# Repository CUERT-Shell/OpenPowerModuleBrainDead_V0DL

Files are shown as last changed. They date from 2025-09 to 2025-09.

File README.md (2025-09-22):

# OpenPowerModule

Kicad Design 
You can view on https://kicanvas.org (for non kicad users)

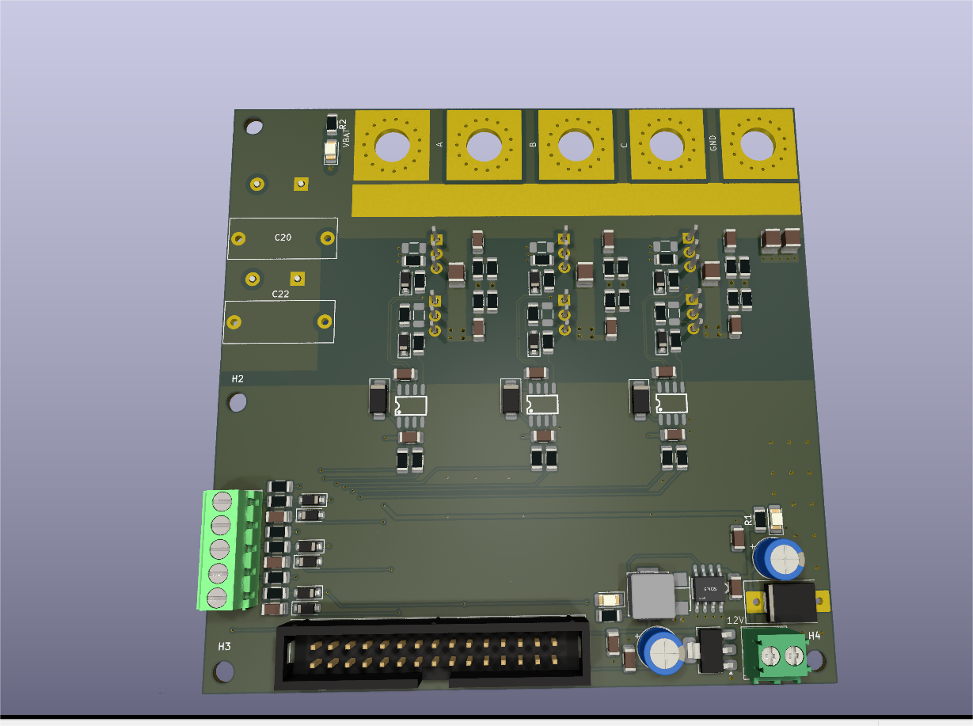
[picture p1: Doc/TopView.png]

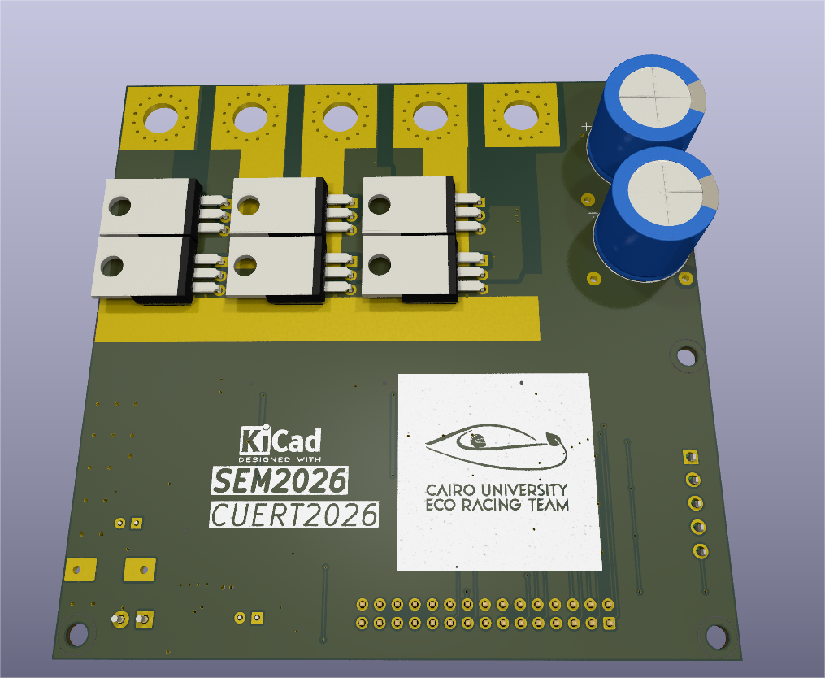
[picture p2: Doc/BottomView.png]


Minimal BLDC drive hardware (without microcontroller)

### The hardware 
* 3phase H-bridge and all its related circuitry (MGD , Snubber , decoupling , etc)
* Hall Sensor Conditioning Circuits
* IDC-2x15 Connector to be interfaced with a controller/MCU
* 12V-->5V buck converter , 3.3V LDO

### Repo Structure
* Main directory : design files
* Production directory : Gerbers and Bom
* LIB : Project Components library
* Doc : Design Reference , guide , step file , etc...

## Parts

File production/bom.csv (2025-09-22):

Designator | Footprint | Quantity | Value | LCSC Part #
C1, C57, C63, C65 | 1206 | 4 | 10u 50V | C13585
C10, C19, C21, C31, C49 | 1210 | 5 | 10uF 100V | C5156756
C12, C2, C3 | 1206 | 3 | 10uF 50V | C7432781
C23, C24, C4, C41, C42, C5 | 1206 | 6 | 470pF | C377098
C27, C29, C44, C45, C7, C9 | 1206 | 6 | 3nF 100V | C7393993
C34, C40, C48 | 1206 | 3 | 220nF 100V | C377088
C61, C67, C69 | 1206 | 3 | 100n 50V | C24497
D10, D11, D19, D20, D26, D27, D28, D29, D5, D6, D7, D8 | D_SOD-123 | 12 | D_Schottky | C181204
D12, D13, D9 | D_SMA | 3 | SS110 | C432299
D16 | SMA_L4.3-W2.6-LS5.2-RD | 1 | SS34_C8678 | C8678
D25, D3, D4 | 1206 | 3 | LED RED | C965822
L1 | IND-SMD_L7.1-W6.6_H5.0 | 1 | SMMS0650-680M | C2894721
Q1, Q2, Q3, Q4, Q5, Q6 | TO-220-3_Horizontal_TabUp | 6 | IRF1407 | C33129604
R1, R10, R2, R21, R22, R31, R32, R45, R51, R54, R9 | 1206 | 11 | 10k | C17902
R13, R14, R15, R16, R19, R20, R25, R26, R27, R28, R29, R3, R30, R35, R36, R37, R38, R4 | 1206 | 18 | 10 | C137208
R17, R18, R46, R5, R52, R55, R6, R7, R8 | 1206 | 9 | 100 | C113307
R53 | 1206 | 1 | 1k | C2907440
U1, U2, U3 | SOP-8_L4.9-W3.9-P1.27-LS6.0-BL | 3 | EG2131_C5240691 | C5240691
U4 | SOIC-8_L5.0-W4.0-P1.27-LS6.0-BL | 1 | XL1509-5.0E1 | C61063
U6 | SOT-223-3_TabPin2 | 1 | AMS1117-3.3 | C347222

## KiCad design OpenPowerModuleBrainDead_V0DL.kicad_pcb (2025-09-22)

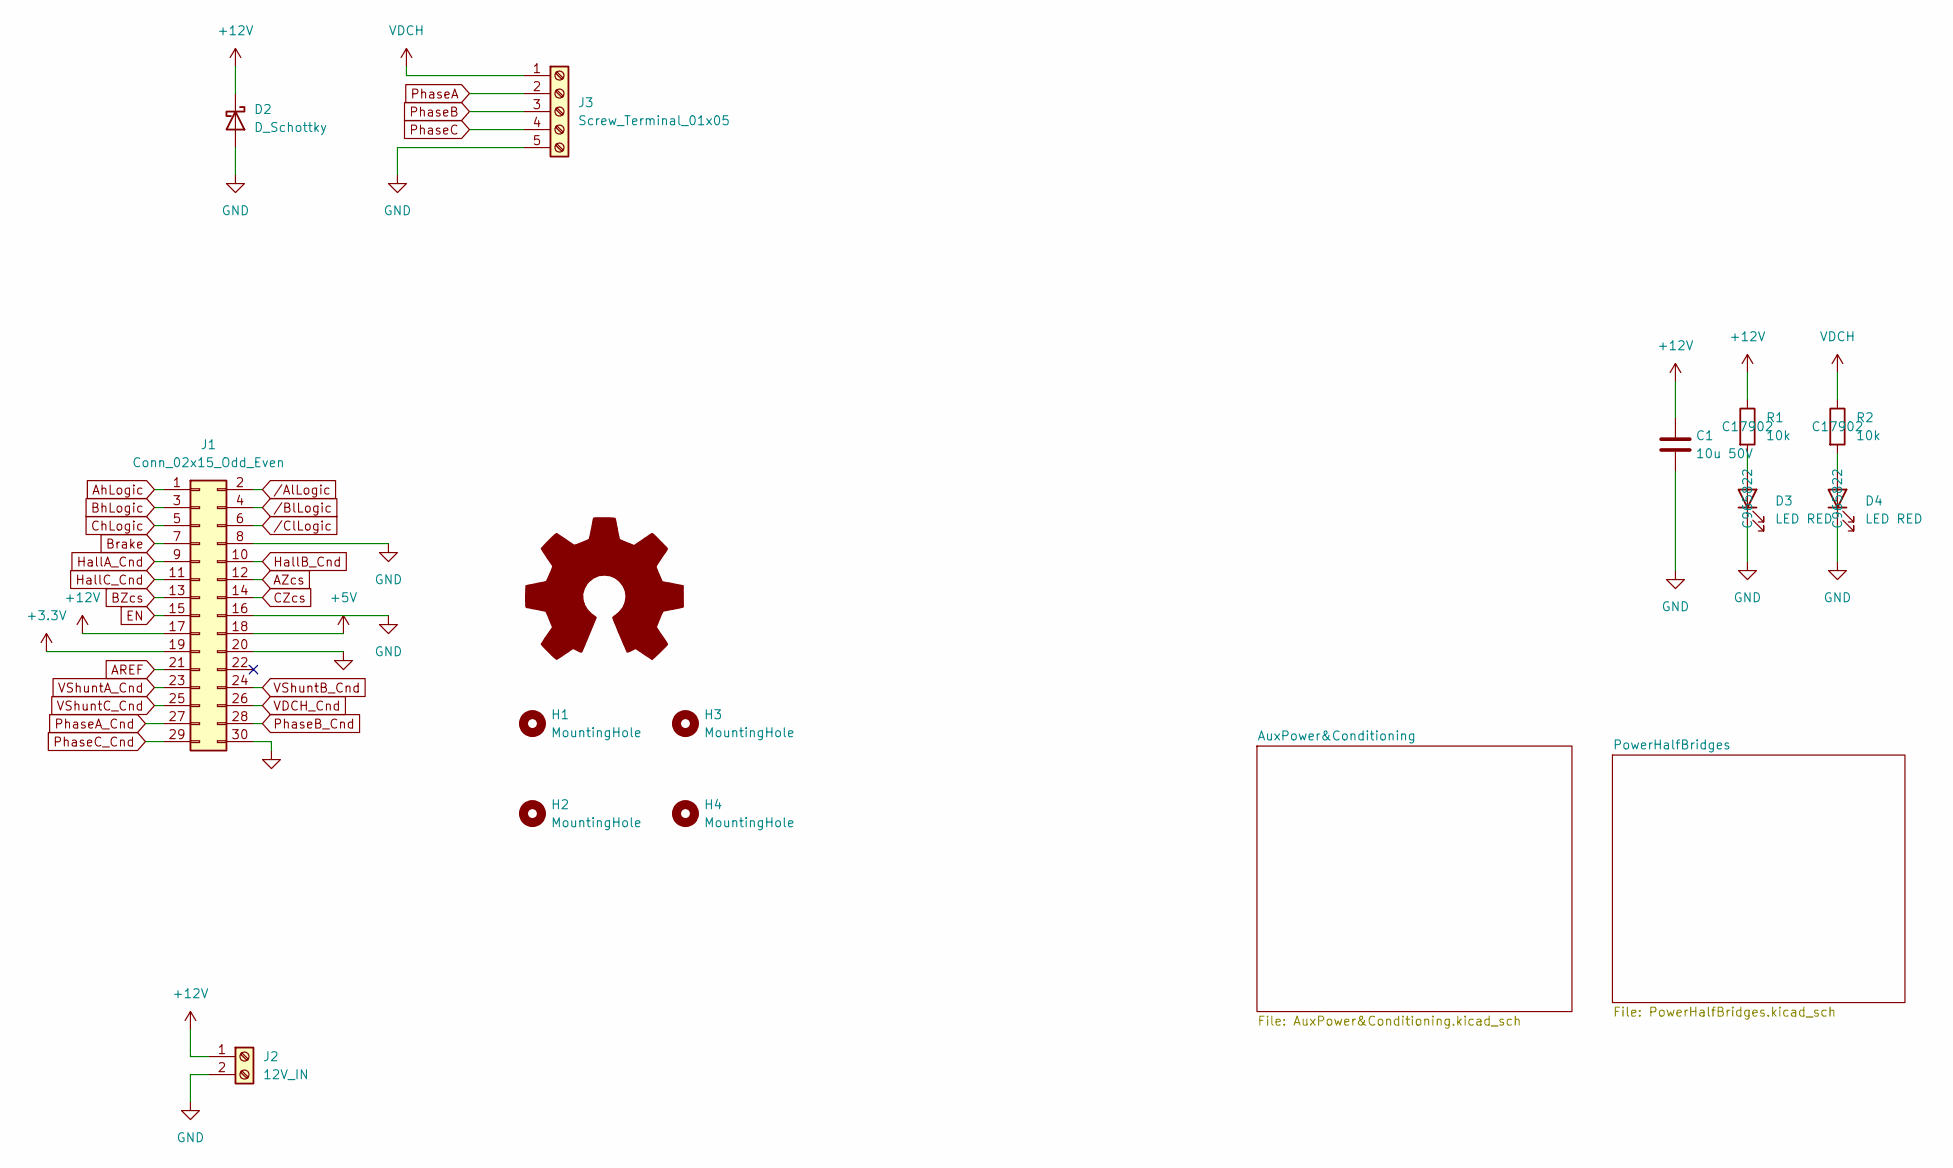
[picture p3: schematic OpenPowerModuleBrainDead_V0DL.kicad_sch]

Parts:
C1: 10u 50V; C_1206_3216Metric; LCSC Part C13585
D2: D_Schottky; D_SMC-RM10_Universal_Handsoldering
D3, D4: LED RED; LED_1206_3216Metric_Pad1.42x1.75mm_HandSolder; LCSC Part C965822
H1, H2, H3, H4: MountingHole; MountingHole_3.2mm_M3_DIN965
H5: Logo_Open_Hardware_Large; MadeWithKicad
J1: Conn_02x15_Odd_Even; IDC-Header_2x15_P2.54mm_Vertical
J2: 12V_IN; TerminalBlock_Phoenix_PT-1,5-2-3.5-H_1x02_P3.50mm_Horizontal
J3: Screw_Terminal_01x05; PowerConn_01x05_P20
R1, R2: 10k; R_1206_3216Metric; LCSC Part C17902

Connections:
+3.3V: J1.19; also elsewhere on the board
+5V: J1.18; also elsewhere on the board
+12V: C1.1, D2.1 (K), J1.17, J2.1, R1.1; also elsewhere on the board
AREF: J1.21
AZcs: J1.12
AhLogic: J1.1; also elsewhere on the board
BZcs: J1.13
BhLogic: J1.3; also elsewhere on the board
Brake: J1.7
CZcs: J1.14
ChLogic: J1.5; also elsewhere on the board
EN: J1.15
GND: C1.2, D2.2 (A), D3.1 (K), D4.1 (K), J1.8, J1.16, J1.20, J1.30, J2.2, J3.5; also elsewhere on the board
HallA_Cnd: J1.9; also elsewhere on the board
HallB_Cnd: J1.10; also elsewhere on the board
HallC_Cnd: J1.11; also elsewhere on the board
unnamed: D3.2 (A), R1.2
unnamed: D4.2 (A), R2.2
PhaseA: J3.2; also elsewhere on the board
PhaseA_Cnd: J1.27
PhaseB: J3.3; also elsewhere on the board
PhaseB_Cnd: J1.28
PhaseC: J3.4; also elsewhere on the board
PhaseC_Cnd: J1.29
VDCH: J3.1, R2.1; also elsewhere on the board
VDCH_Cnd: J1.26
VShuntA_Cnd: J1.23
VShuntB_Cnd: J1.24
VShuntC_Cnd: J1.25
/AlLogic: J1.2; also elsewhere on the board
/BlLogic: J1.4; also elsewhere on the board
/ClLogic: J1.6; also elsewhere on the board

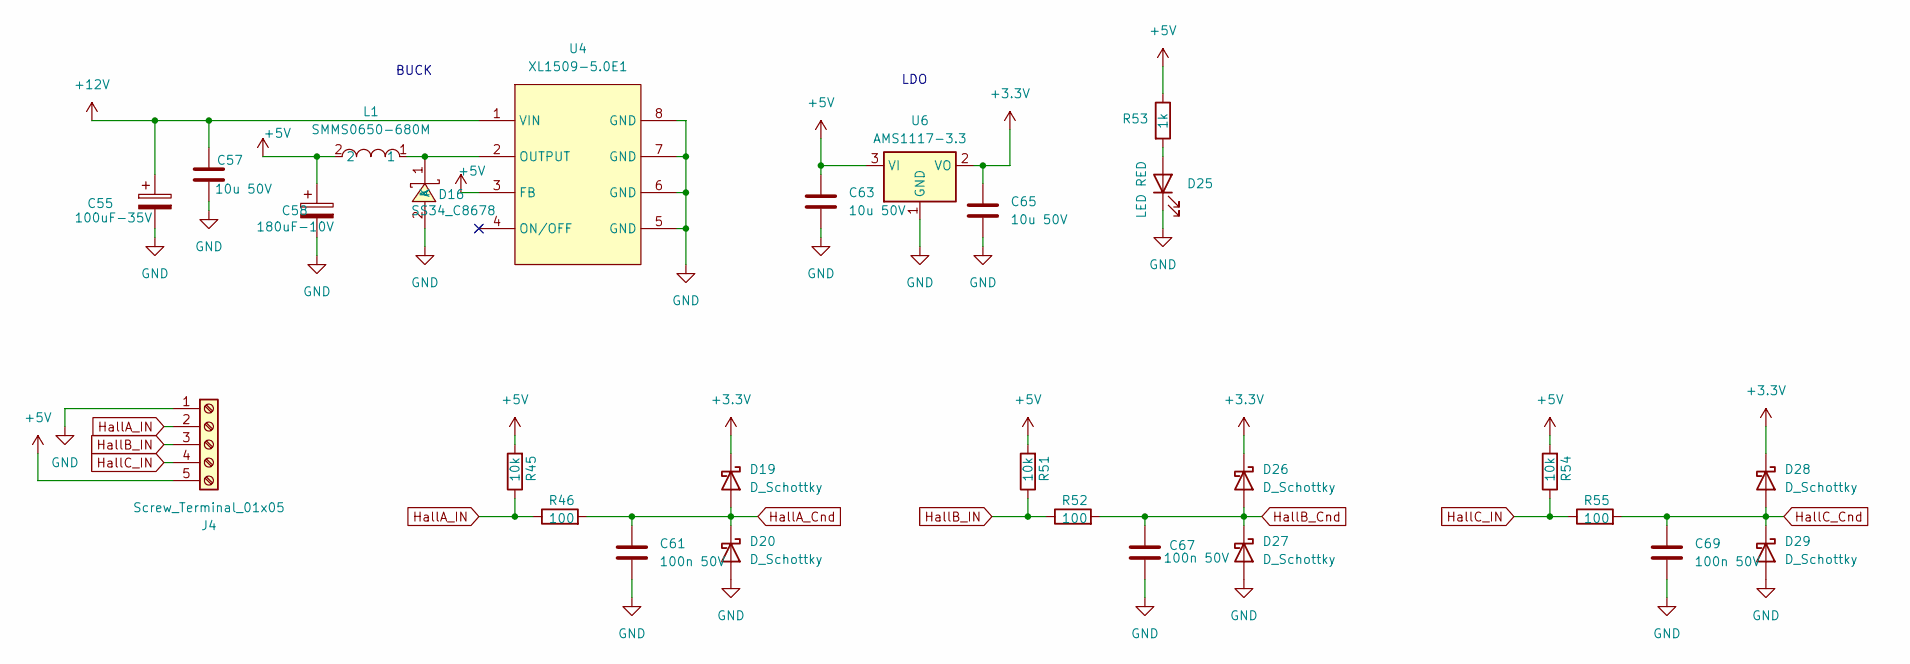
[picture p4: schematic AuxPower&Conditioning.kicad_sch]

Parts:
C55: 100uF-35V; CP_Radial_D6.3mm_P2.50mm
C57, C63, C65: 10u 50V; C_1206_3216Metric; LCSC Part C13585
C58: 180uF-10V; CP_Radial_D6.3mm_P2.50mm
C61, C67, C69: 100n 50V; C_1206_3216Metric; LCSC Part C24497
D16: SS34_C8678; SMA_L4.3-W2.6-LS5.2-RD; LCSC Part C8678
D19, D20, D26, D27, D28, D29: D_Schottky; D_SOD-123; LCSC Part C181204
D25: LED RED; LED_1206_3216Metric_Pad1.42x1.75mm_HandSolder; LCSC Part C965822
J4: Screw_Terminal_01x05; CONN-TH_5P-P3.50_DORABO_DB125-3.5-5P-GN-S
L1: SMMS0650-680M; IND-SMD_L7.1-W6.6_H5.0; LCSC Part C2894721
R45, R51, R54: 10k; R_1206_3216Metric; LCSC Part C17902
R46, R52, R55: 100; R_1206_3216Metric; LCSC Part C113307
R53: 1k; R_1206_3216Metric; LCSC Part C2907440
U4: XL1509-5.0E1; SOIC-8_L5.0-W4.0-P1.27-LS6.0-BL; LCSC Part C61063
U6: AMS1117-3.3; SOT-223-3_TabPin2; LCSC Part C347222

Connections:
+3.3V: C65.1, D19.1 (K), D26.1 (K), D28.1 (K), U6.2 (VO); also elsewhere on the board
+5V: C58.1, C63.1, J4.5, L1.2, R45.2, R51.2, R53.1, R54.2, U4.3 (FB), U6.3 (VI); also elsewhere on the board
+12V: C55.1, C57.1, U4.1 (VIN); also elsewhere on the board
GND: C55.2, C57.2, C58.2, C61.2, C63.2, C65.2, C67.2, C69.2, D16.2 (A), D20.2 (A), D25.1 (K), D27.2 (A), D29.2 (A), J4.1, U4.5 (GND), U4.6 (GND), U4.7 (GND), U4.8 (GND), U6.1 (GND); also elsewhere on the board
HallA_Cnd: C61.1, D19.2 (A), D20.1 (K), R46.2; also elsewhere on the board
HallA_IN: J4.2, R45.1, R46.1
HallB_Cnd: C67.1, D26.2 (A), D27.1 (K), R52.2; also elsewhere on the board
HallB_IN: J4.3, R51.1, R52.1
HallC_Cnd: C69.1, D28.2 (A), D29.1 (K), R55.2; also elsewhere on the board
HallC_IN: J4.4, R54.1, R55.1
unnamed: D16.1 (K), L1.1, U4.2 (OUTPUT)
unnamed: D25.2 (A), R53.2

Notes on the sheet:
LDO
BUCK

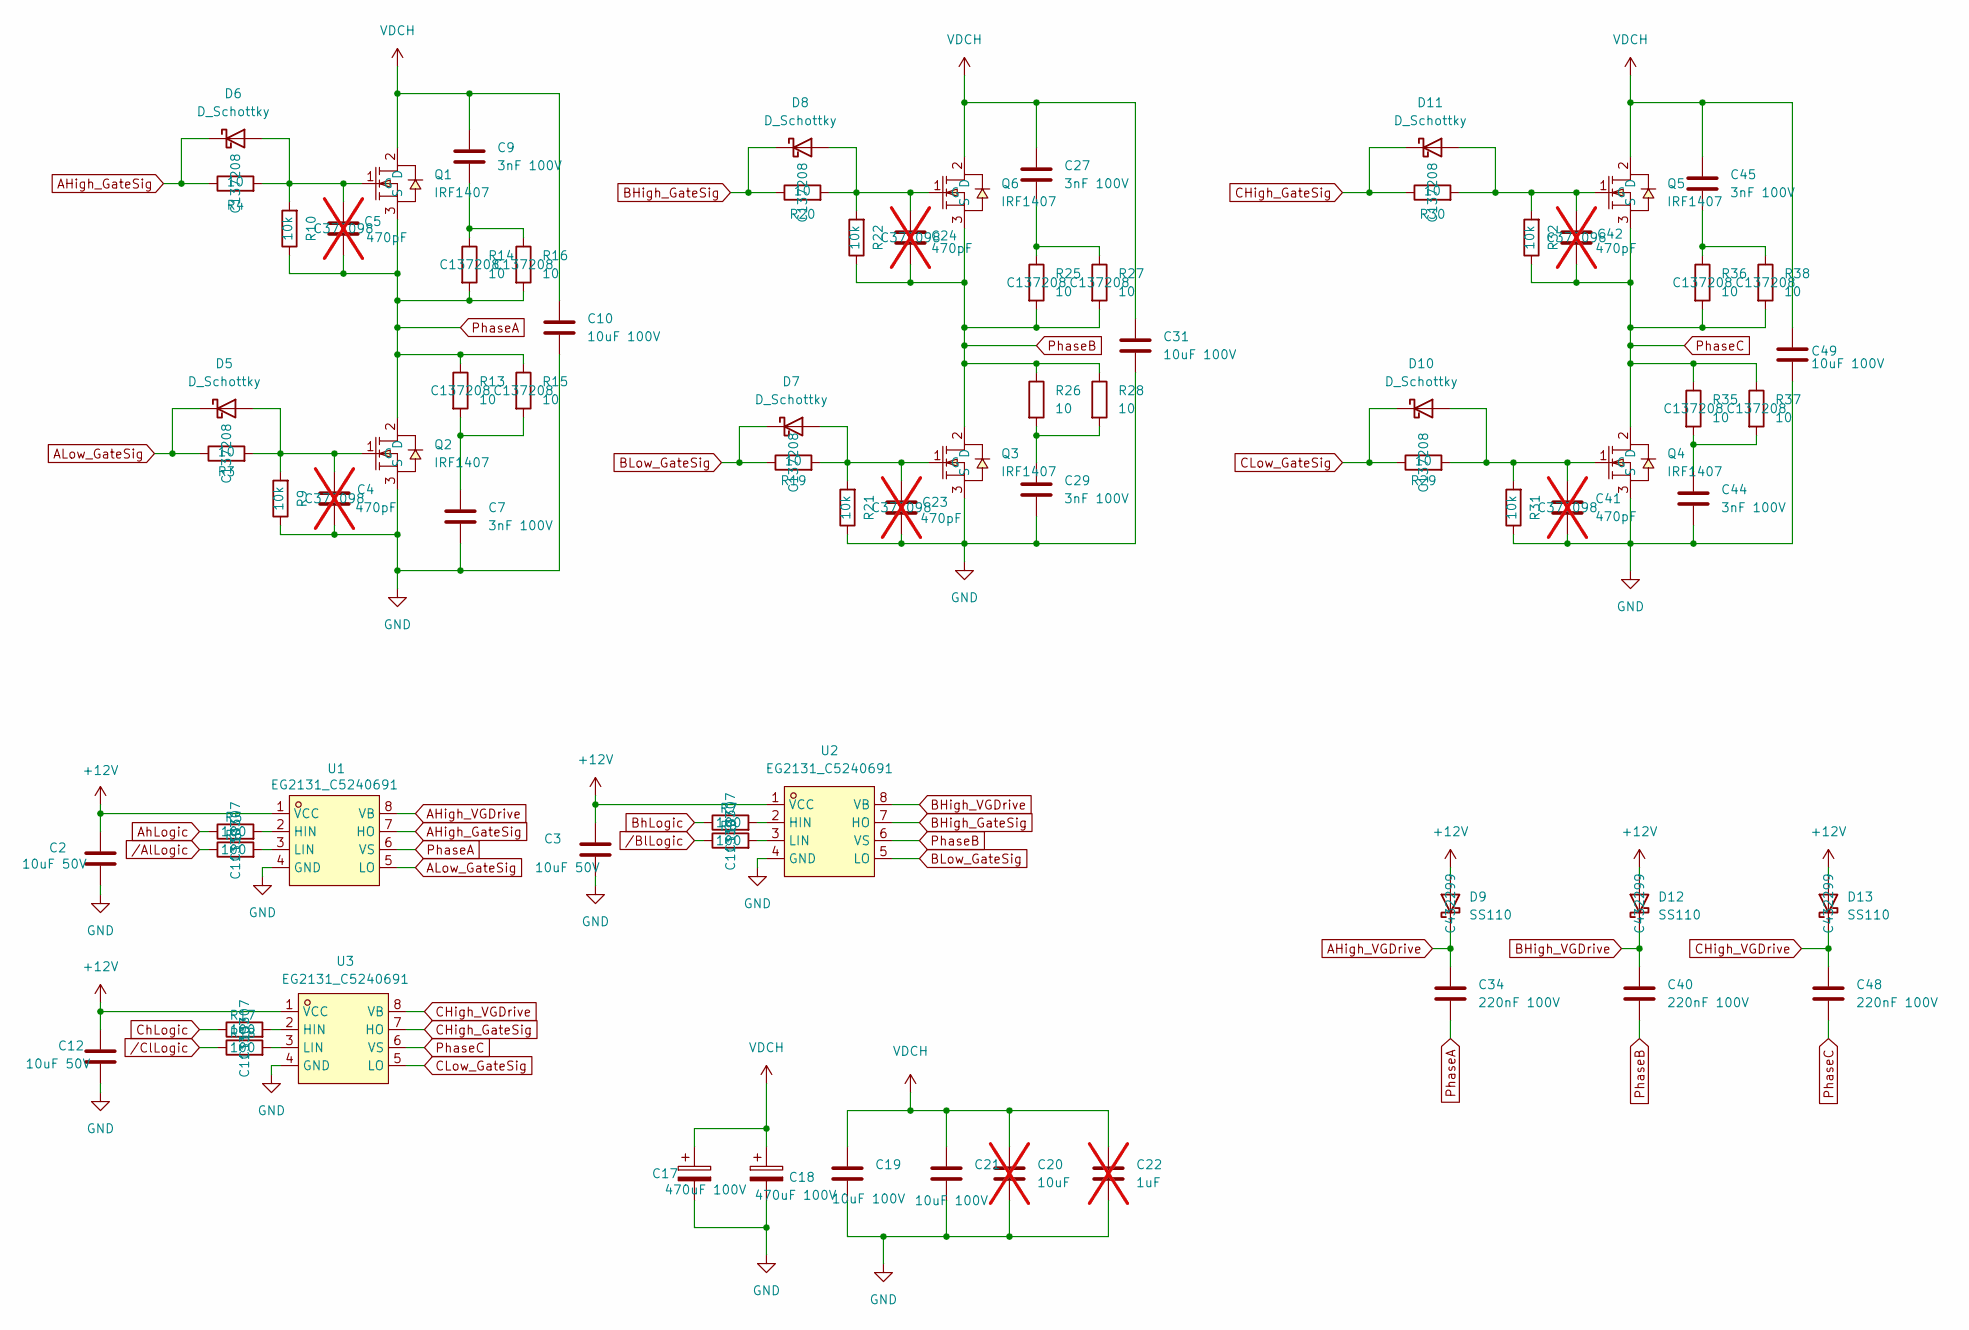
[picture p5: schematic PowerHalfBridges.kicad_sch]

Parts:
C2, C3, C12: 10uF 50V; C_1206_3216Metric; LCSC Part C7432781
C4, C5, C23, C24, C41, C42: 470pF; C_1206_3216Metric; LCSC Part C377098; not fitted
C7, C9, C27, C29, C44, C45: 3nF 100V; C_1206_3216Metric; LCSC Part C7393993
C10, C19, C21, C31, C49: 10uF 100V; C_1210_3225Metric; LCSC Part C5156756
C17, C18: 470uF 100V; CP_Radial_D16.0mm_P7.50mm
C20: 10uF; C_Rect_L18.0mm_W7.0mm_P15.00mm_FKS3_FKP3; not fitted
C22: 1uF; C_Rect_L18.0mm_W7.0mm_P15.00mm_FKS3_FKP3; not fitted
C34, C40, C48: 220nF 100V; C_1206_3216Metric; LCSC Part C377088
D5, D6, D7, D8, D10, D11: D_Schottky; D_SOD-123; LCSC Part C181204
D9, D12, D13: SS110; D_SMA; LCSC Part C432299
Q1, Q2, Q3, Q4, Q5, Q6: IRF1407; TO-220-3_Horizontal_TabUp; LCSC Part C33129604
R3, R4, R13, R14, R15, R16, R19, R20, R25, R26, R27, R28, R29, R30, R35, R36, R37, R38: 10; R_1206_3216Metric; LCSC Part C137208
R5, R6, R7, R8, R17, R18: 100; R_1206_3216Metric; LCSC Part C113307
R9, R10, R21, R22, R31, R32: 10k; R_1206_3216Metric; LCSC Part C17902
U1, U2, U3: EG2131_C5240691; SOP-8_L4.9-W3.9-P1.27-LS6.0-BL; LCSC Part C5240691

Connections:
+12V: C2.1, C3.1, C12.1, D9.2 (A), D12.2 (A), D13.2 (A), U1.1 (VCC), U2.1 (VCC), U3.1 (VCC); also elsewhere on the board
AHigh_GateSig: D6.1 (K), R4.1, U1.7 (HO)
AHigh_VGDrive: C34.1, D9.1 (K), U1.8 (VB)
ALow_GateSig: D5.1 (K), R3.1, U1.5 (LO)
AhLogic: R5.1; also elsewhere on the board
BHigh_GateSig: D8.1 (K), R20.1, U2.7 (HO)
BHigh_VGDrive: C40.1, D12.1 (K), U2.8 (VB)
BLow_GateSig: D7.1 (K), R19.1, U2.5 (LO)
BhLogic: R7.1; also elsewhere on the board
CHigh_GateSig: D11.1 (K), R30.1, U3.7 (HO)
CHigh_VGDrive: C48.1, D13.1 (K), U3.8 (VB)
CLow_GateSig: D10.1 (K), R29.1, U3.5 (LO)
ChLogic: R17.1; also elsewhere on the board
GND: C2.2, C3.2, C4.2, C7.2, C10.2, C12.2, C17.2, C18.2, C19.2, C20.2, C21.2, C22.2, C23.2, C29.2, C31.2, C41.2, C44.2, C49.2, Q2.3 (S), Q3.3 (S), Q4.3 (S), R9.1, R21.1, R31.1, U1.4 (GND), U2.4 (GND), U3.4 (GND); also elsewhere on the board
unnamed: C7.1, R13.2, R15.2
unnamed: C9.2, R14.1, R16.1
unnamed: C27.2, R25.1, R27.1
unnamed: C29.1, R26.2, R28.2
unnamed: C44.1, R35.2, R37.2
unnamed: C45.2, R36.1, R38.1
unnamed: C4.1, D5.2 (A), Q2.1 (G), R3.2, R9.2
unnamed: C5.1, D6.2 (A), Q1.1 (G), R4.2, R10.2
unnamed: C23.1, D7.2 (A), Q3.1 (G), R19.2, R21.2
unnamed: C24.1, D8.2 (A), Q6.1 (G), R20.2, R22.2
unnamed: C41.1, D10.2 (A), Q4.1 (G), R29.2, R31.2
unnamed: C42.1, D11.2 (A), Q5.1 (G), R30.2, R32.2
unnamed: R5.2, U1.2 (HIN)
unnamed: R6.2, U1.3 (LIN)
unnamed: R7.2, U2.2 (HIN)
unnamed: R8.2, U2.3 (LIN)
unnamed: R17.2, U3.2 (HIN)
unnamed: R18.2, U3.3 (LIN)
PhaseA: C5.2, C34.2, Q1.3 (S), Q2.2 (D), R10.1, R13.1, R14.2, R15.1, R16.2, U1.6 (VS); also elsewhere on the board
PhaseB: C24.2, C40.2, Q3.2 (D), Q6.3 (S), R22.1, R25.2, R26.1, R27.2, R28.1, U2.6 (VS); also elsewhere on the board
PhaseC: C42.2, C48.2, Q4.2 (D), Q5.3 (S), R32.1, R35.1, R36.2, R37.1, R38.2, U3.6 (VS); also elsewhere on the board
VDCH: C9.1, C10.1, C17.1, C18.1, C19.1, C20.1, C21.1, C22.1, C27.1, C31.1, C45.1, C49.1, Q1.2 (D), Q5.2 (D), Q6.2 (D); also elsewhere on the board
/AlLogic: R6.1; also elsewhere on the board
/BlLogic: R8.1; also elsewhere on the board
/ClLogic: R18.1; also elsewhere on the board

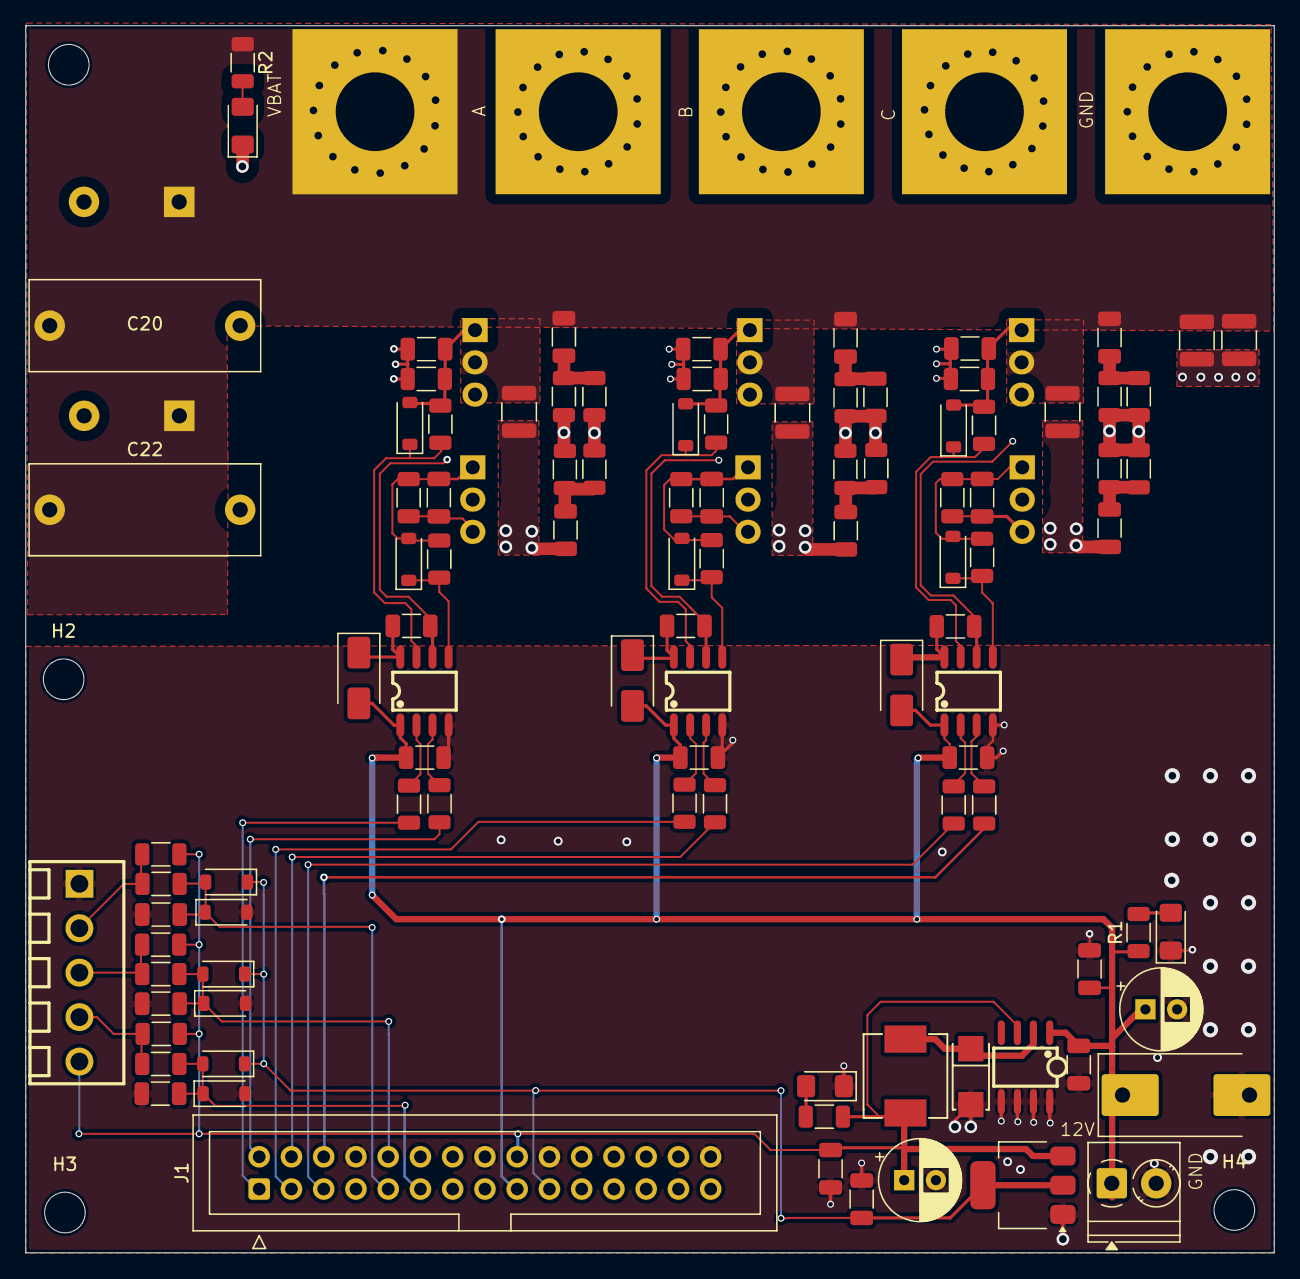
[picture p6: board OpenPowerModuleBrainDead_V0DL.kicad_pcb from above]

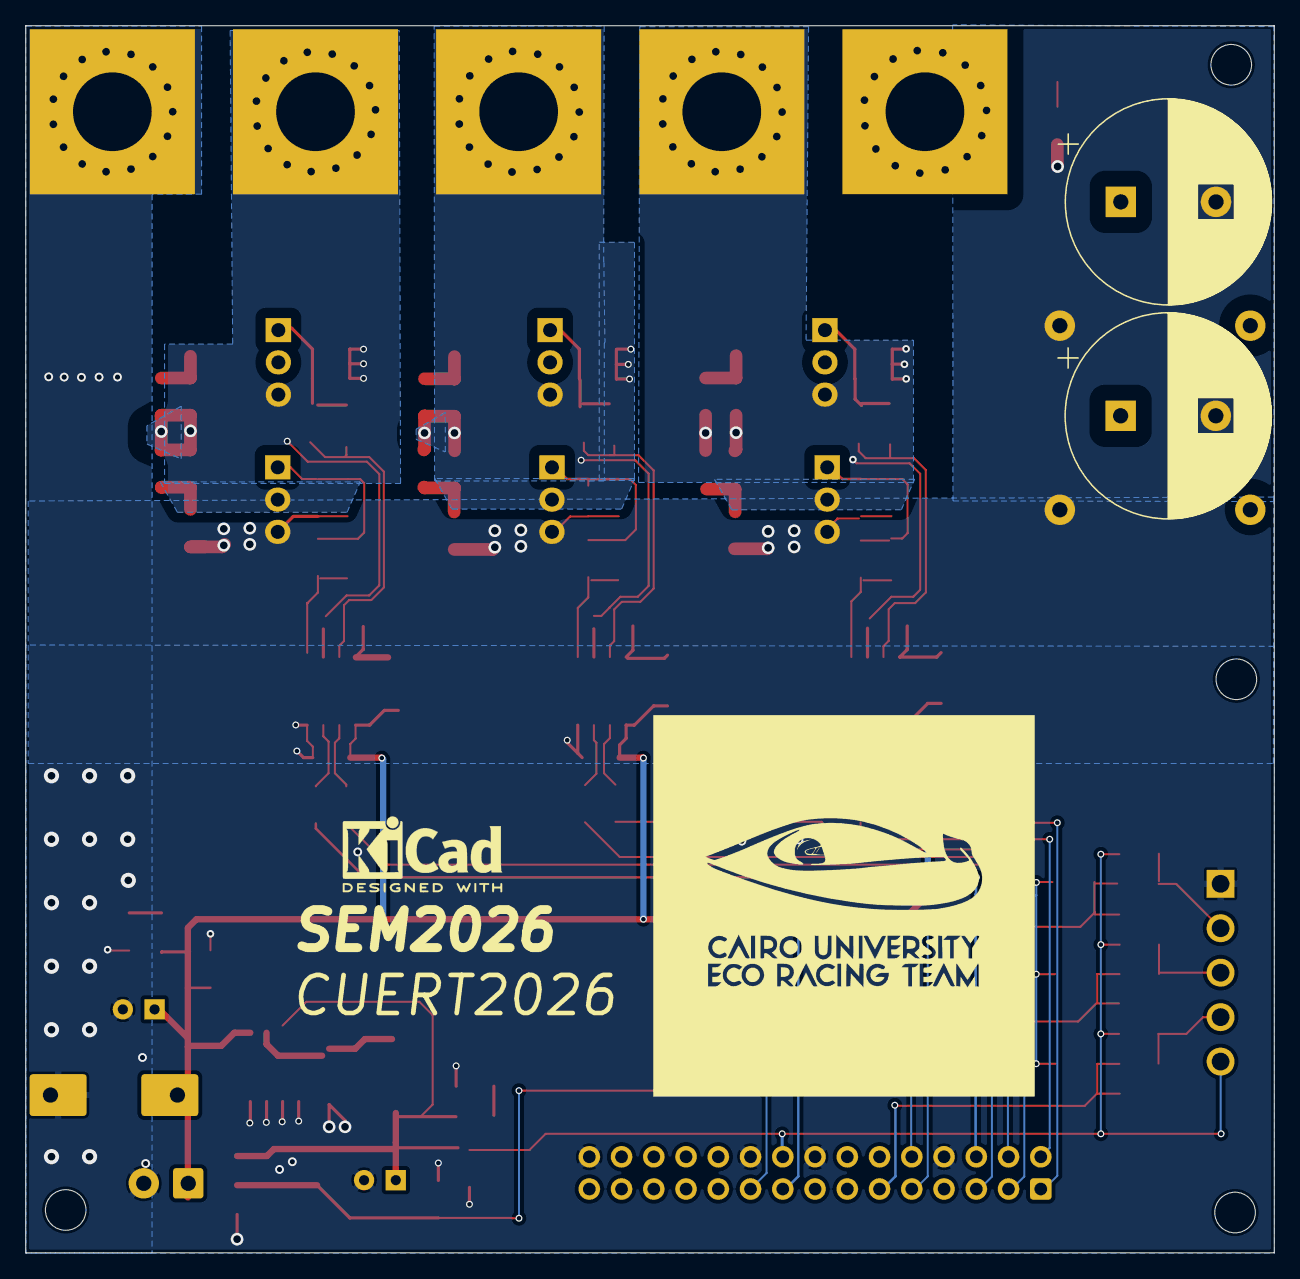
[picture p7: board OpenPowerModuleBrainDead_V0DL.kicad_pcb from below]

Board: 2 copper layers, 98.3 x 96.6 mm, 116 parts (9 on the bottom side), 51 nets.
